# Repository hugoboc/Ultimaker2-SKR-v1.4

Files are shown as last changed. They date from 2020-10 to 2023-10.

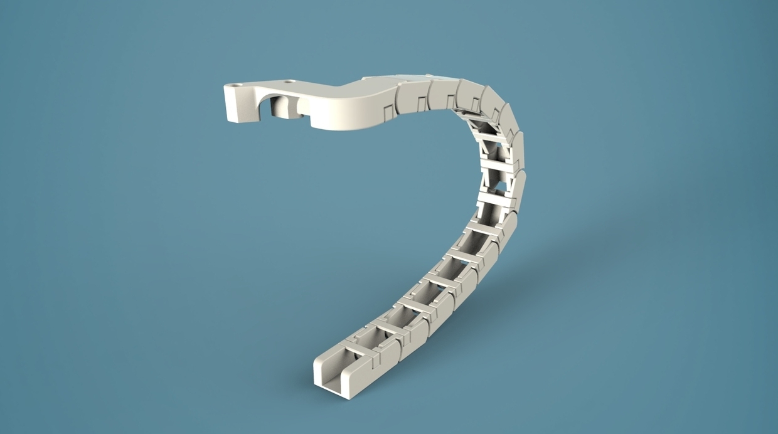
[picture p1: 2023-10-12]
01 CAD/03_z_stage_assembly/Ultimaker 2 Cable Chain/photos/UM2CC.jpg

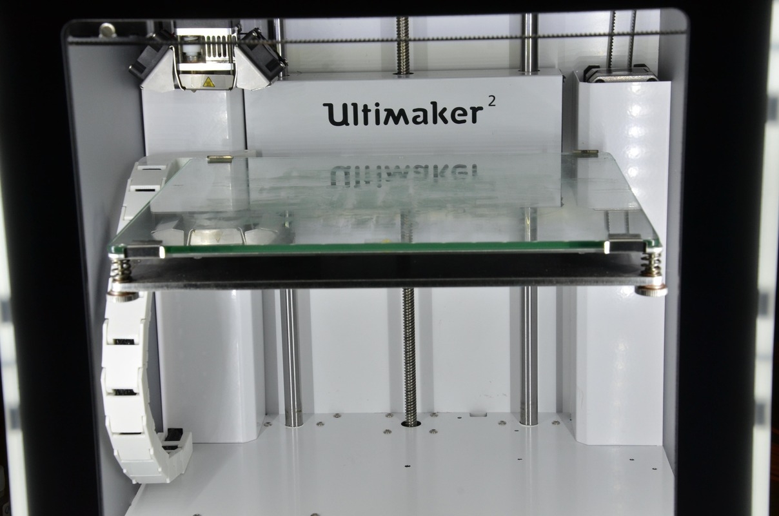
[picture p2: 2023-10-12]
01 CAD/03_z_stage_assembly/Ultimaker 2 Cable Chain/photos/um2_energyChain.jpg

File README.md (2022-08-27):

# Ultimaker 2 SKR v1.4 Turbo
all documentation needed to update Ultimaker 2 with a Bigtreetech SKR v1.4 32 bit board 

Features:

- HextrudOrt direct drive
- Optimized bed base plate to minimize vibrations
- 8mm print head shafts
- Custom sliding blocks
- Magnetic spring steel plate
- Z Probe for bed mesh leveling
- Klipper firmware

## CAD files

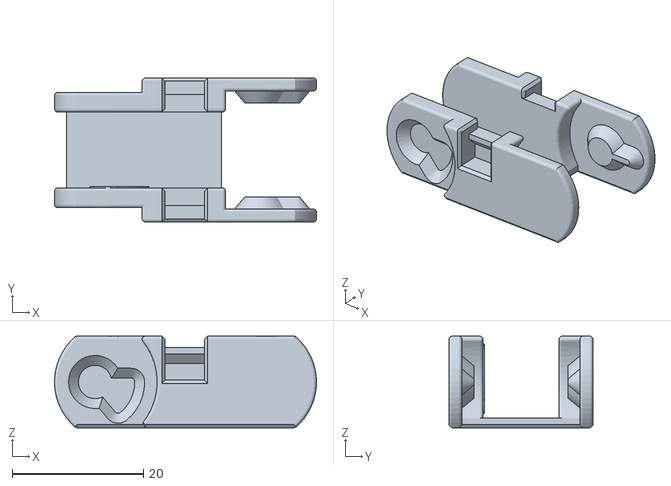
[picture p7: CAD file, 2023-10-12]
01 CAD/03_z_stage_assembly/Ultimaker 2 Cable Chain/UM2CableChain_ChainSegment.STL
40.0 x 22.0 x 14.0

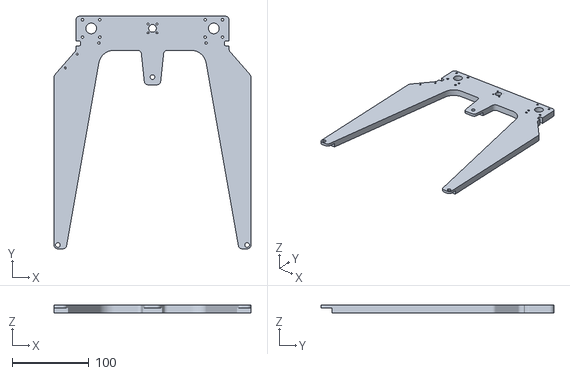
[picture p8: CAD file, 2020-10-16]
05 STLs/base_plate_optimized_10mm.stl
257.0 x 303.5 x 10.0

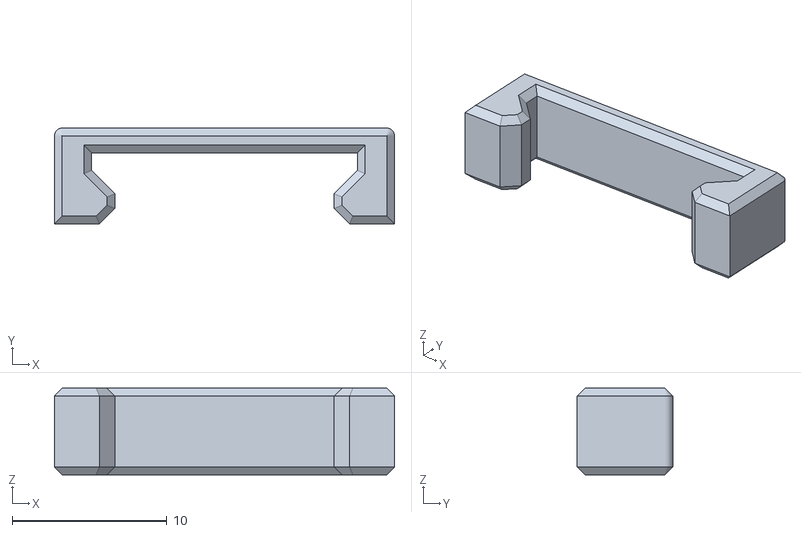
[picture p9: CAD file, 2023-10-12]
01 CAD/03_z_stage_assembly/Ultimaker 2 Cable Chain/UM2CableChain_Lid.STL
22.0 x 6.20 x 5.60

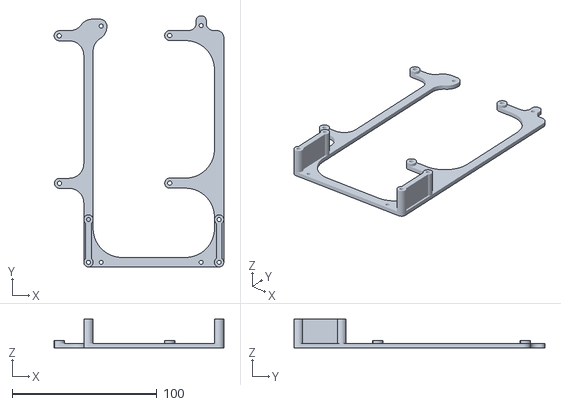
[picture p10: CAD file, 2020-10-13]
05 STLs/um2_skr14_holder.stl
117.2 x 173.2 x 20.0

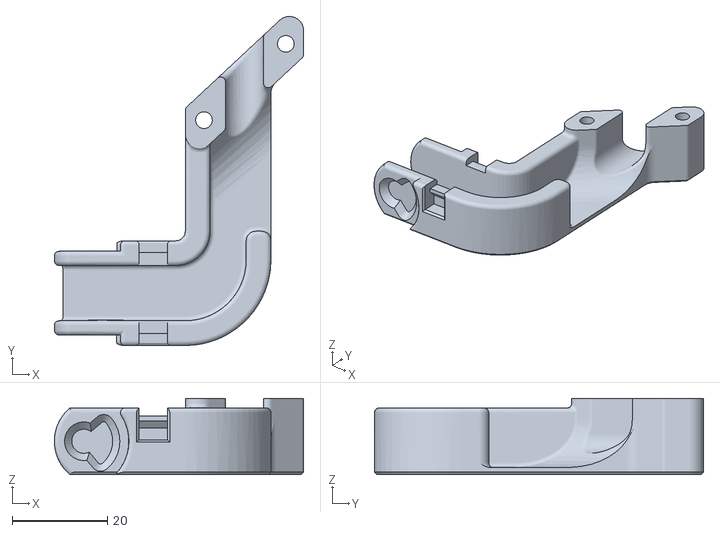
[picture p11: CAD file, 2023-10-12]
01 CAD/03_z_stage_assembly/Ultimaker 2 Cable Chain/UM2CableChain_BedEnd.STL
52.4 x 69.1 x 16.0

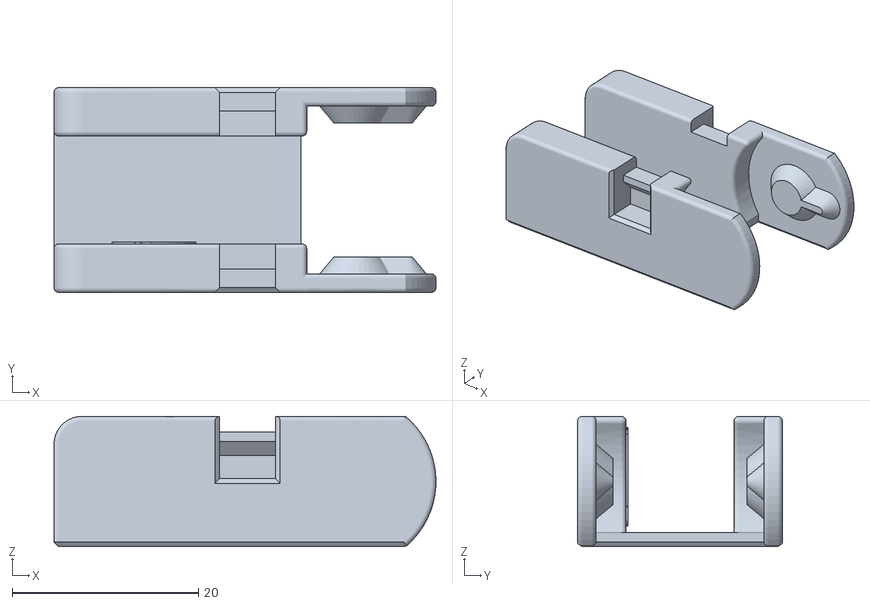
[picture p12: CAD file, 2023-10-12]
01 CAD/03_z_stage_assembly/Ultimaker 2 Cable Chain/UM2CableChain_BottomEnd.STL
41.0 x 22.0 x 14.0

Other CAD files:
01 CAD/03_z_stage_assembly/z-stage_assembly_2 v13.f3z

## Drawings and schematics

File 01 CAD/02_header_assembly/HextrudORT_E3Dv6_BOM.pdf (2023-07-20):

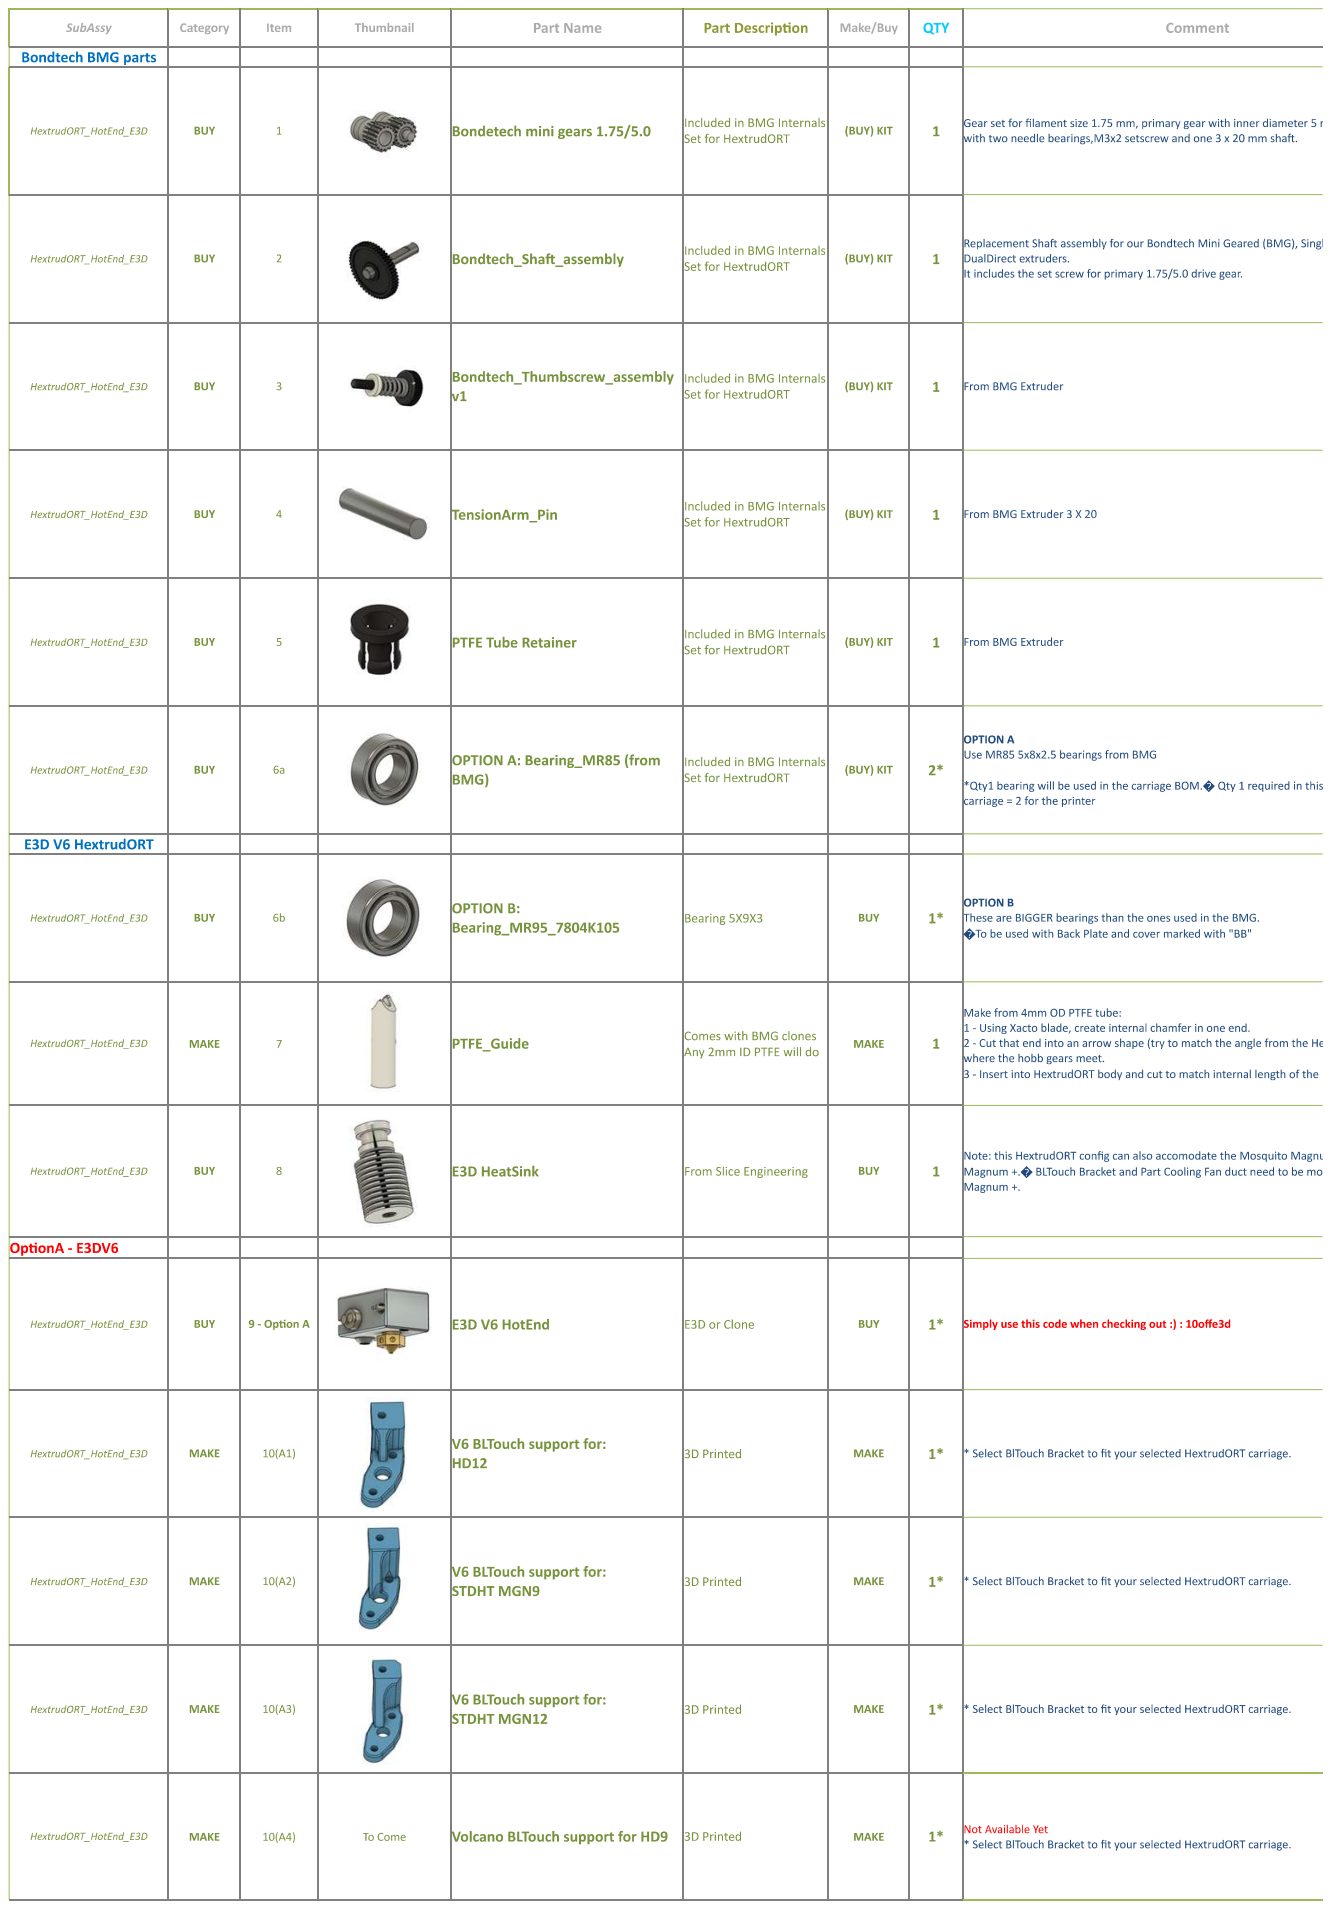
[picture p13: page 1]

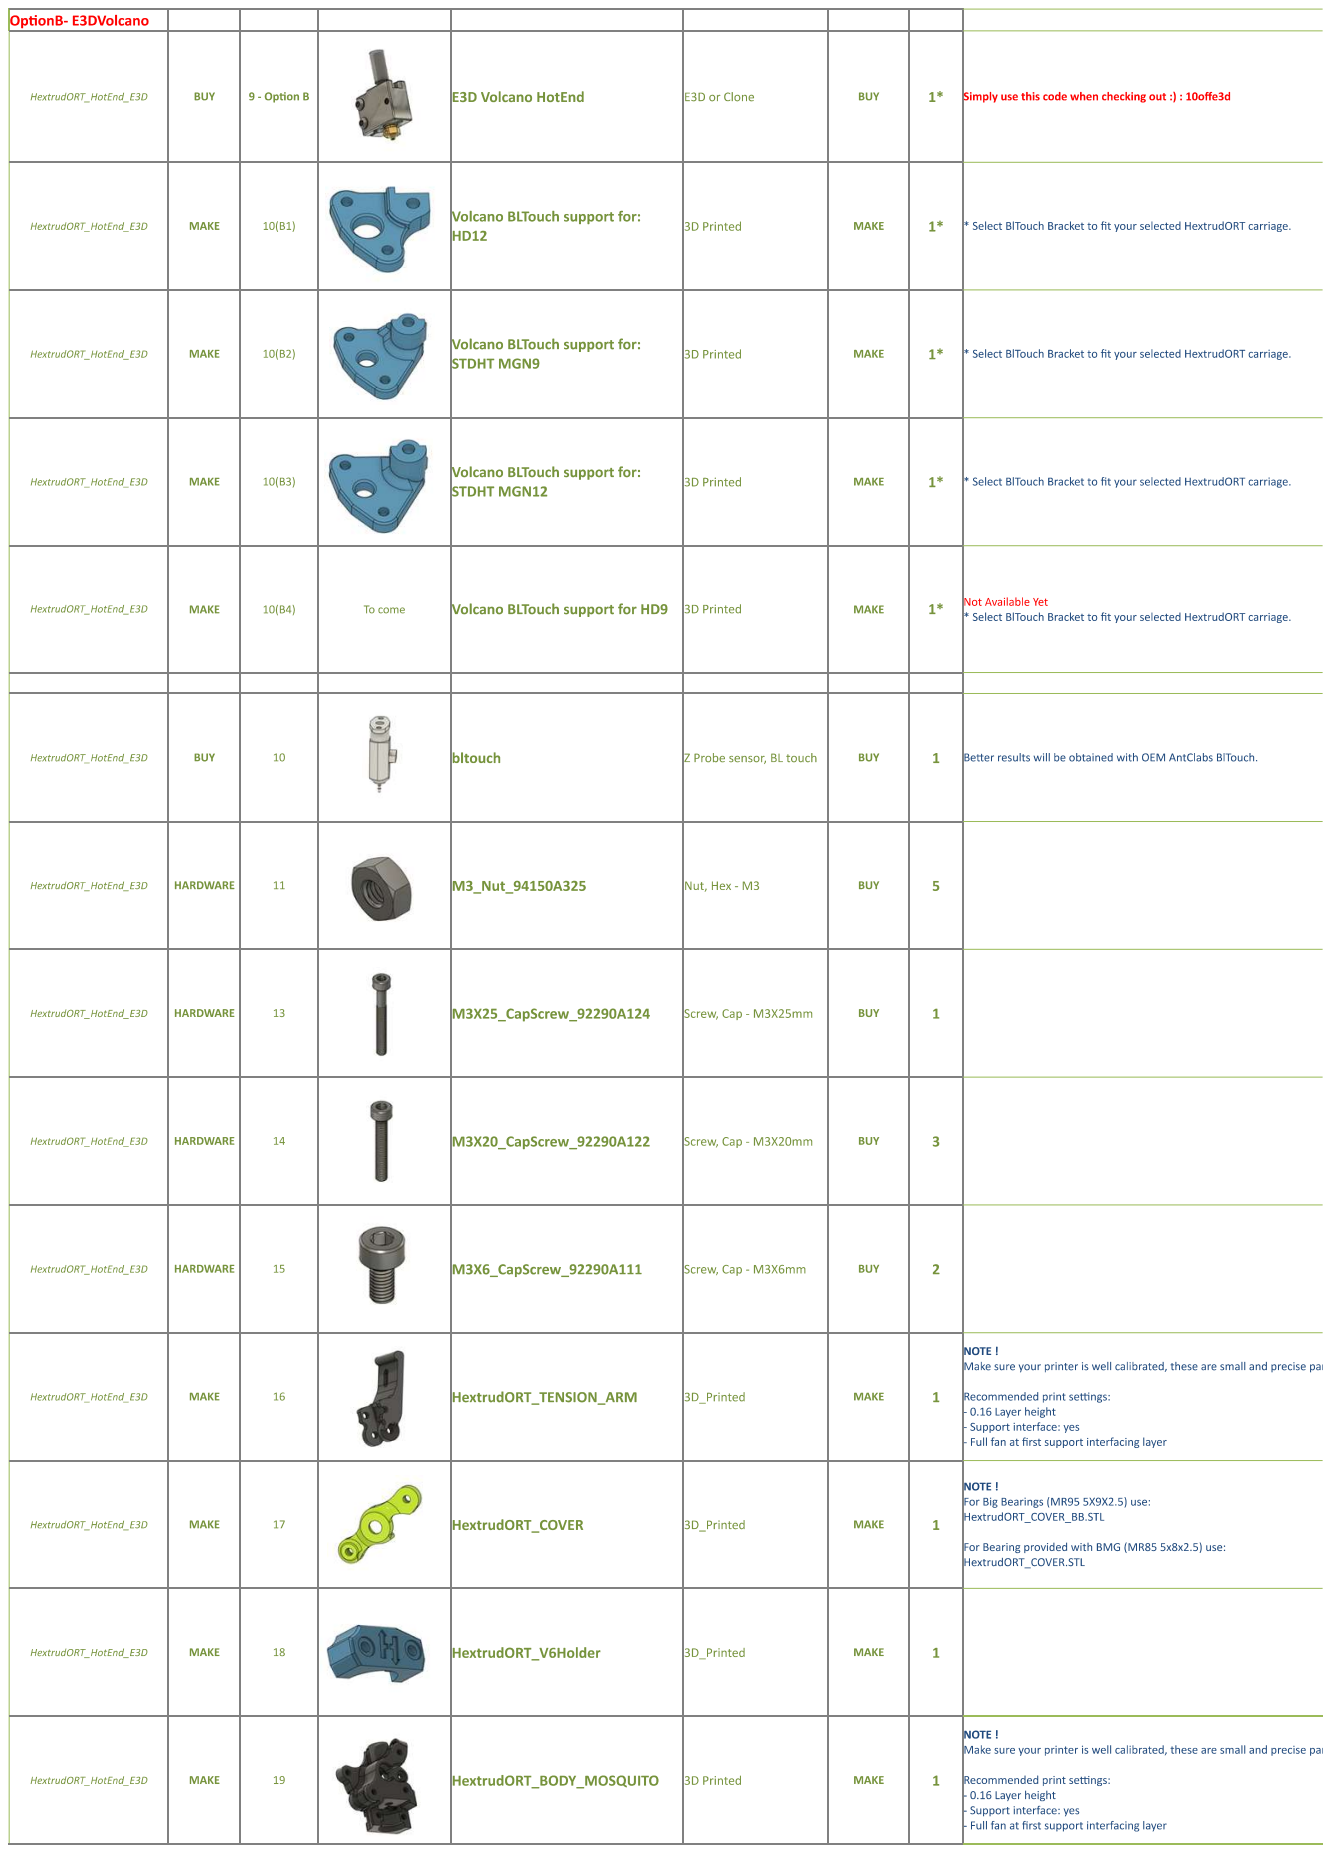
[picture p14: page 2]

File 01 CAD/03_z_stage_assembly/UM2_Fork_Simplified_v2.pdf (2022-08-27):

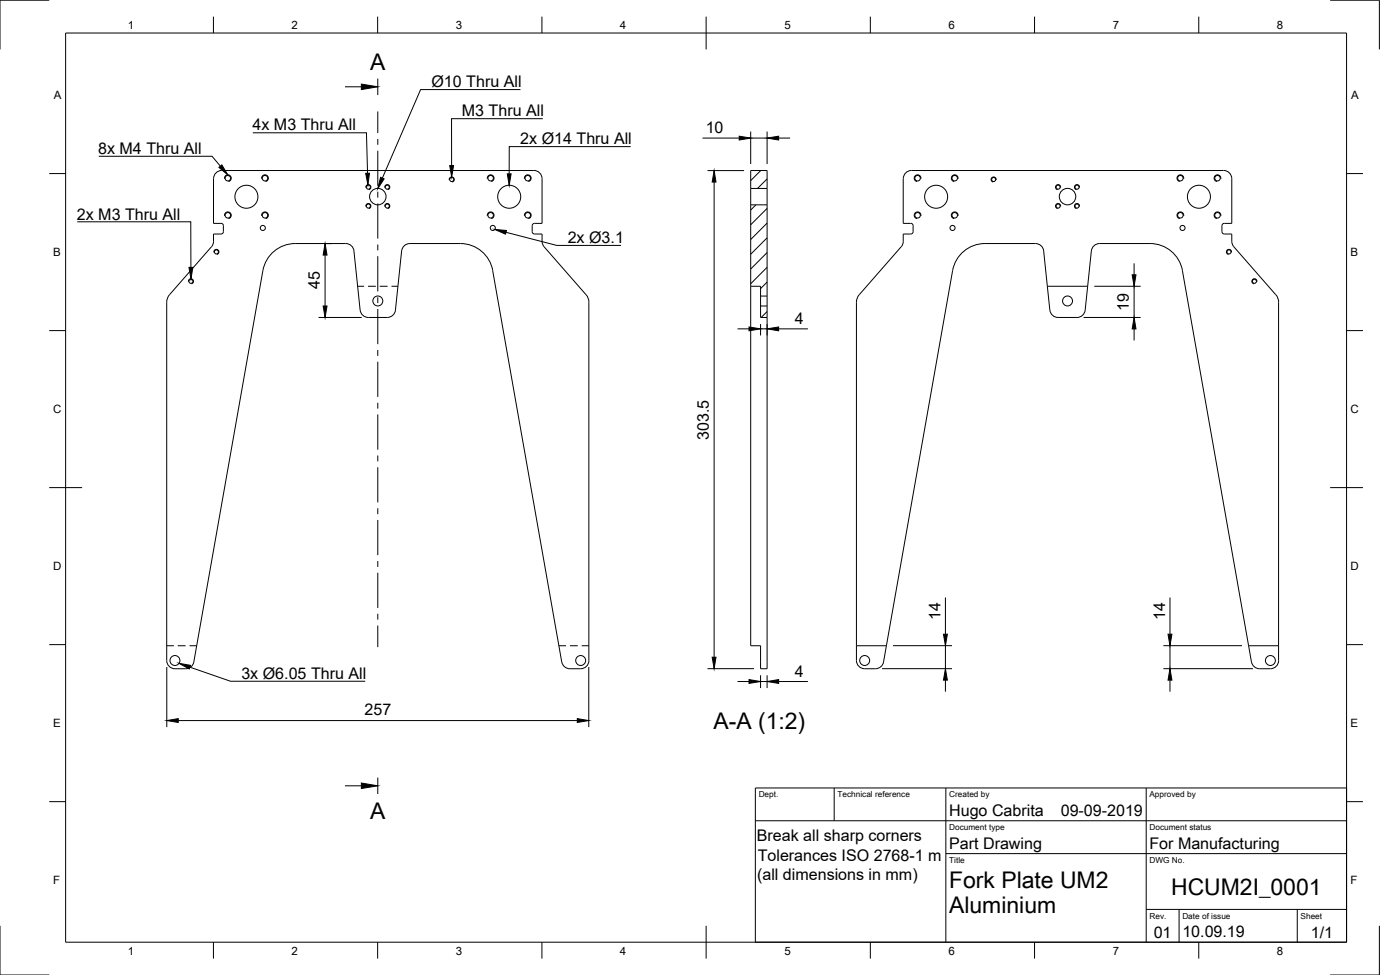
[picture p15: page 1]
8x M4 Thru All; 2x M3 Thru All; 3x Ø6.05 Thru All; 2x Ø14 Thru All; M3 Thru All; Ø10 Thru All; 4x M3 Thru All

Dept. | Technical reference | Created by Hugo Cabrita 09-09-2019 | Approved by

Break all sharp corners Tolerances ISO 2768-1 m (all dimensions in mm) | | Document type Part Drawing | Document status For Manufacturing

Title Fork Plate UM2 Aluminium | DWG No. HCUM2I_0001

Rev. 01 | Date of issue 10.09.19 | Sheet 1/1

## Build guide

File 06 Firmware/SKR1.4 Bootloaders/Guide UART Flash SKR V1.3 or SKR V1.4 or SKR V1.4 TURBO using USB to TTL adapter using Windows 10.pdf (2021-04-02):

Version 1.0 by GadgetAngel based on Sineos work

Just for future reference: Flashed a SKR 1.4 Turbo with @ardiehl Bootloader, using a USB to TTL adapter:
Things needed:
USB to TTL adapter, e.g. https://www.amazon.com/dp/B075N82CDL Some Jumper wires, e.g https://www.amazon.com/dp/B01EV70C78 female to female for the USB to TTL
female to male to conveniently contact the pin P2.10 to get the board into ISP mode
@ardiehl bootloader hex (attached to this post, or build it your self) (https://github.com/GadgetAngel/BTT_SKR_13_14_14T_SD-DFU-Bootloader/tree/main/bootloader_bin/compiled_bootloader_bin) Flashmagic (https://www.flashmagictool.com/download.html)
Procedure:
1. Power the board via USB or 12V / 24V
2. Contact the USB TTL adapter as shown in the picture (cyan arrows) RX of the adapter to TX on the board
TX of the adapter to RX on the board
GND to GND
3. Contact the SMD resistor (R28) to GND of the board (dark blue arrows), e.g. middle pin of an endstop (here the female to male jumper cable comes in handy). This will connect to the ISP_BOOT mode pin P2.10 (contact- Nr3).
4. Reset the board while holding the contact (Nr. 3)
5. Shortly after releasing the Reset button also remove the ISP connection (Nr. 3)
6. Start Flashmagic
Chose the @ardiehl hex file (https://github.com/GadgetAngel/BTT_SKR_13_14_14T_SD-DFU-Bootloader/tree/main/bootloader_bin/compiled_bootloader_bin)

# Sineos commented 15 days ago:

## How to backup and restore SKR 1.4 /turbo & SKR 1.3 boards

## Using a USB to TTL Adapter:

Guide to backup and restore SKR 1.4 / turbo (1.3 also work) via UART by USB to TTL adapter. Useful to try to fix corrupted
boot loader and no update from SD problem or simply backup. I, GadgetAngel, have tried to find other ways of doing this with the LPC1768 or LPC1769 and the only method that works is using the embedded boot loader and USART0 communication. I could never get an ST-LINK-V2 clone to work!

(I’m not responsible for any damage, do so at your own risk)

ORIGINAL URL: https://github.com/bigtreetech/BIGTREETECH-SKR-V1.3/issues/346#issuecomment-754120640

Set the correct COM port for your USB to TTL adapter (look it up in the windows device manager)
Set the correct chip type (LPC1769 for SKR 1.4 Turbo)
Set Erase to Sectors used by file
Press start
7. Wait until finished, then reset the board
8. Flash new firmware.bin , e.g. via SD card upload or using the new bootloader's direct flash capabilities
Flashing via STLink v2 did not work for me, neither from linux shell, nor via PlatformIO but the Flashmagic way was surprisingly painless.

# Bootloader Hex (unzip to use):

DFU-Bootloader.zip (https://github.com/bigtreetech/BIGTREETECH-SKR-V1.3/files/5766031/DFU-Bootloader.zip)

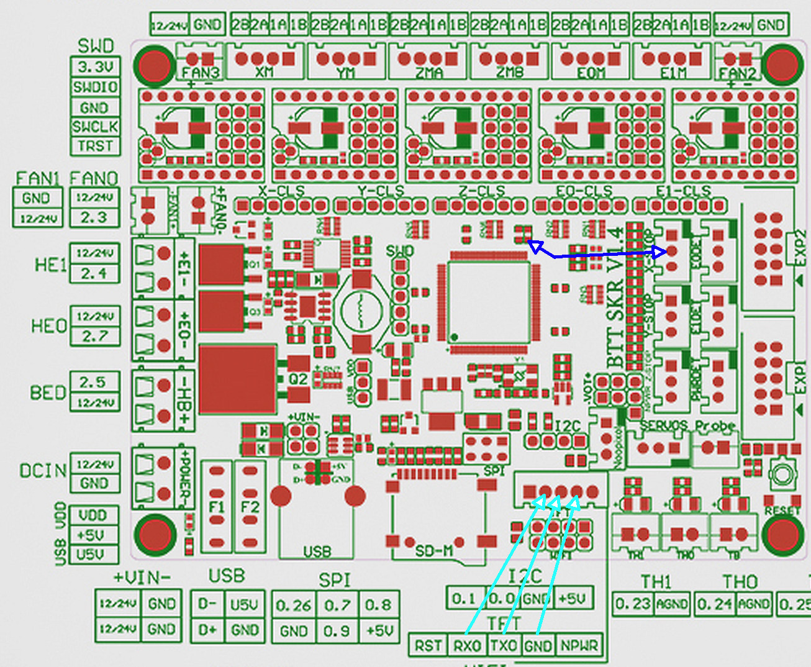
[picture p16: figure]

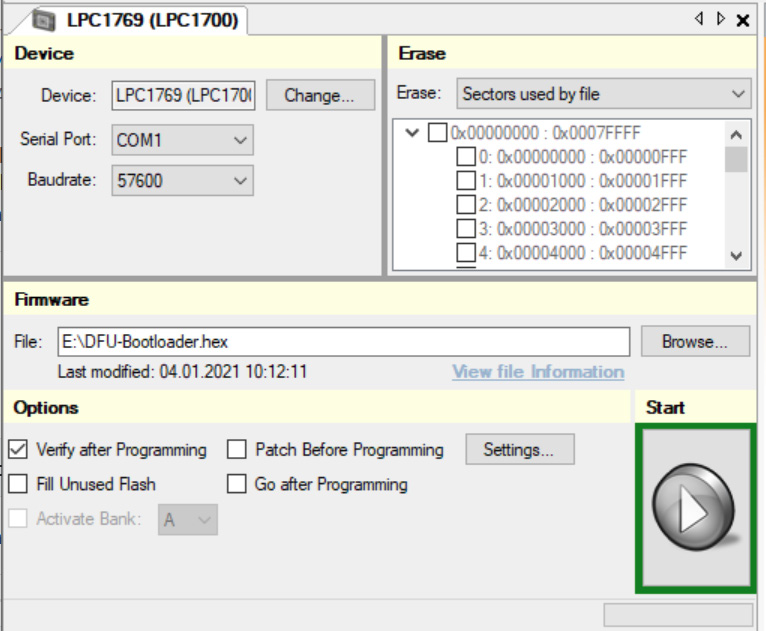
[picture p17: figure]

## Edit for SKR Board 1.3: For SKR 1.3 simply connect AUX-1 in Step 2 and use (read short) the

BOOT Jumper pins to achieve the same as in Step 3 to 5.

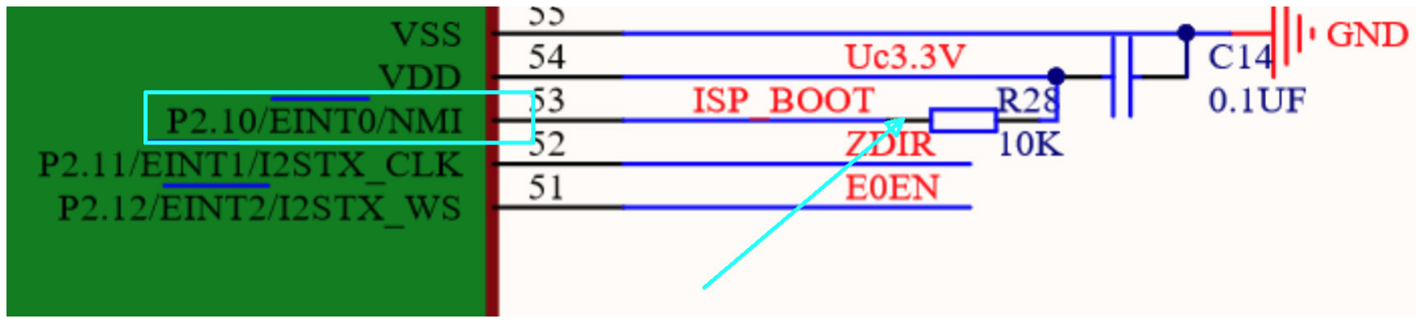
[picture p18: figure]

- So you need to make this contact between GND and P2.10 and hold it, reset the board and then quickly after releasing the reset button remove the contact.

## - To get the chip into the ISP mode you need to pull the pin P2.10 to GND during reset

- The P2.10 is easily accessible via the bottom of the SMD resistor
- GND is easily accessible via, e.g. the middle endstop pin

# IMPORTANT: It needs further explanation about ISP_BOOT PIN needing to be held to low during a board reset so the embedded boot loader will become active:

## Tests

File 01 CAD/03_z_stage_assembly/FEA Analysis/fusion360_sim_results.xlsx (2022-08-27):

Part Name | Material | displacement 2.1N | displacement 2.1N change | displacement 300g | displacement 300g change | modal frequency 1 | modal frequency change | Part Weight | weight change
Original 4mm | Aluminium 6061 | 1.190 | - | 0.170 | - | 39 | - | 0.797 | -
Original 10mm | Aluminium 6061 | 0.079 | -93.33613445% | 0.011 | -93.52941176% | 97 | 148.7179487% | 1.993 | 150.0627353%
Optimized (V3) Alu - 10mm | Aluminium 6061 | 0.220 | -81.51260504% | 0.031 | -81.76470588% | 133 | 241.025641% | 0.797 | 0%
Optimized (V3) Alu - 8mm | Aluminium 6061 | 0.426 | -64.20168067% | 0.061 | -64.11764706% | 107 | 174.3589744% | 0.612 | -23.21204517%
Optimized (V3) Steel - 10mm | Steel - High Strength | 0.076 | -93.62184874% | 0.011 | -93.64705882% | 132 | 238.4615385% | 2.226 | 179.2973651%
Optimized (V3) Steel - 8mm | Steel - High Strength | 0.147 | -87.63865546% | 0.021 | -87.64705882% | 106 | 171.7948718% | 1.781 | 123.4629862%

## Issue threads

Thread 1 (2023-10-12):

follow up questions

totoantibes, 2023-10-12:
Hi this is a very interesting build indeed. i have a few basic questions though.

1) I saw [here](https://community.ultimaker.com/topic/30786-ultimaker-with-skr-14/) that people had to splice the LCD cable in order to get it the correct 3.3 Voltage. Is that not needed? or is that achieved with jumpers somewhere?
2) is there a need for the UM2 Power USB Power Switch adapter interface in order to keep the "holes" on the original case for the power, switch  and usb plug?
3) the UM2 PT100 can then be plugged directly onto the board without amp circuit?

Merci

hugoboc, 2023-10-12:
Hi @totoantibes,

1. I am using Klipper, so I don't use an LCD anymore. I use the Mainsail web interface on my PC or phone to interact with the printer.
2. You don't need one, and I don't think they are for sale anymore (I bought it on Aliexpress). At the time I wanted to keep on using the original UM2 power brick, so I opted for this solution. Now, you'll probably have to buy a power source, but in this case, I think you'll need to modify the "holes" in the back.
3. Yes, but I bought new thermistors (bed and hotend), which I connected directly to the SKR1.4. I've updated the documentation and added which thermistors I have installed.

Documentation in the repo is not so well organized and some things are missing. I'll do some housekeeping in the next few days.

De rien :)

Let me know if you have any more questions.

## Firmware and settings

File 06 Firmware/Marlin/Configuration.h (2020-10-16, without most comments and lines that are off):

#pragma once
#define CONFIGURATION_H_VERSION 020007
#define STRING_CONFIG_H_AUTHOR "(Hugo Cabrita SKR1.4 03.10.2020)" // Who made the changes.
#define SHOW_BOOTSCREEN
#define SERIAL_PORT -1
#define SERIAL_PORT_2 0
#define BAUDRATE 250000
  #define MOTHERBOARD BOARD_BTT_SKR_V1_4_TURBO
#define CUSTOM_MACHINE_NAME "UM2 SKR1.4"
#define EXTRUDERS 1
#define DEFAULT_NOMINAL_FILAMENT_DIA 1.75
#define TEMP_SENSOR_0 5
#define TEMP_SENSOR_1 0
#define TEMP_SENSOR_2 0
#define TEMP_SENSOR_3 0
#define TEMP_SENSOR_4 0
#define TEMP_SENSOR_5 0
#define TEMP_SENSOR_6 0
#define TEMP_SENSOR_7 0
#define TEMP_SENSOR_BED 5
#define TEMP_SENSOR_PROBE 0
#define TEMP_SENSOR_CHAMBER 0
#define DUMMY_THERMISTOR_998_VALUE 25
#define DUMMY_THERMISTOR_999_VALUE 100
#define MAX_REDUNDANT_TEMP_SENSOR_DIFF 10
#define TEMP_RESIDENCY_TIME     10  // (seconds) Time to wait for hotend to "settle" in M109
#define TEMP_WINDOW              1  // (°C) Temperature proximity for the "temperature reached" timer
#define TEMP_HYSTERESIS          3  // (°C) Temperature proximity considered "close enough" to the target
#define TEMP_BED_RESIDENCY_TIME 10  // (seconds) Time to wait for bed to "settle" in M190
#define TEMP_BED_WINDOW          1  // (°C) Temperature proximity for the "temperature reached" timer
#define TEMP_BED_HYSTERESIS      3  // (°C) Temperature proximity considered "close enough" to the target
#define HEATER_0_MINTEMP   5
#define HEATER_1_MINTEMP   5
#define HEATER_2_MINTEMP   5
#define HEATER_3_MINTEMP   5
#define HEATER_4_MINTEMP   5
#define HEATER_5_MINTEMP   5
#define HEATER_6_MINTEMP   5
#define HEATER_7_MINTEMP   5
#define BED_MINTEMP        5
#define HEATER_0_MAXTEMP 255
#define HEATER_1_MAXTEMP 275
#define HEATER_2_MAXTEMP 275
#define HEATER_3_MAXTEMP 275
#define HEATER_4_MAXTEMP 275
#define HEATER_5_MAXTEMP 275
#define HEATER_6_MAXTEMP 275
#define HEATER_7_MAXTEMP 275
#define BED_MAXTEMP      100
#define PIDTEMP
#define BANG_MAX 255     // Limits current to nozzle while in bang-bang mode; 255=full current
#define PID_MAX BANG_MAX // Limits current to nozzle while PID is active (see PID_FUNCTIONAL_RANGE below); 255=full current
#define PID_K1 0.95      // Smoothing factor within any PID loop
    #define DEFAULT_Kp  22.20
    #define DEFAULT_Ki   1.08
    #define DEFAULT_Kd 114.00
#define MAX_BED_POWER 255 // limits duty cycle to bed; 255=full current
  #define PID_FUNCTIONAL_RANGE 10 // If the temperature difference between the target temperature and the actual temperature
#define PREVENT_COLD_EXTRUSION
#define EXTRUDE_MINTEMP 170
#define PREVENT_LENGTHY_EXTRUDE
#define EXTRUDE_MAXLENGTH 200
#define THERMAL_PROTECTION_HOTENDS // Enable thermal protection for all extruders
#define THERMAL_PROTECTION_BED     // Enable thermal protection for the heated bed
#define THERMAL_PROTECTION_CHAMBER // Enable thermal protection for the heated chamber
#define USE_XMIN_PLUG
#define USE_YMAX_PLUG
#define USE_ZMAX_PLUG
#define ENDSTOPPULLUPS
#define X_MIN_ENDSTOP_INVERTING false // Set to true to invert the logic of the endstop.
#define Y_MIN_ENDSTOP_INVERTING false // Set to true to invert the logic of the endstop.
#define Z_MIN_ENDSTOP_INVERTING true // Set to true to invert the logic of the endstop.
#define X_MAX_ENDSTOP_INVERTING false // Set to true to invert the logic of the endstop.
#define Y_MAX_ENDSTOP_INVERTING false // Set to true to invert the logic of the endstop.
#define Z_MAX_ENDSTOP_INVERTING true // Set to true to invert the logic of the endstop.
#define Z_MIN_PROBE_ENDSTOP_INVERTING true // Set to true to invert the logic of the probe.
#define X_DRIVER_TYPE  TMC2209
#define Y_DRIVER_TYPE  TMC2209
#define Z_DRIVER_TYPE  TMC2209
#define E0_DRIVER_TYPE TMC2209
#define DEFAULT_AXIS_STEPS_PER_UNIT   { 80, 80, 200, 805.68 }
#define DEFAULT_MAX_FEEDRATE          { 300, 300, 40, 45 }
#define DEFAULT_MAX_ACCELERATION      { 500, 500, 100, 10000 }
#define DEFAULT_ACCELERATION          3000    // X, Y, Z and E acceleration for printing moves
#define DEFAULT_RETRACT_ACCELERATION  3000    // E acceleration for retracts
#define DEFAULT_TRAVEL_ACCELERATION   3000    // X, Y, Z acceleration for travel (non printing) moves
#define DEFAULT_EJERK    5.0  // May be used by Linear Advance
  #define JUNCTION_DEVIATION_MM 0.013 // (mm) Distance from real junction edge
  #define JD_HANDLE_SMALL_SEGMENTS    // Use curvature estimation instead of just the junction angle
#define Z_MIN_PROBE_USES_Z_MIN_ENDSTOP_PIN
#define NOZZLE_TO_PROBE_OFFSET { 10, 10, 0 }
#define PROBING_MARGIN 10
#define XY_PROBE_SPEED (133*60)
#define Z_PROBE_SPEED_FAST HOMING_FEEDRATE_Z
#define Z_PROBE_SPEED_SLOW (Z_PROBE_SPEED_FAST / 2)
#define Z_CLEARANCE_DEPLOY_PROBE   10 // Z Clearance for Deploy/Stow
#define Z_CLEARANCE_BETWEEN_PROBES  5 // Z Clearance between probe points
#define Z_CLEARANCE_MULTI_PROBE     5 // Z Clearance between multiple probes
#define Z_PROBE_LOW_POINT          -2 // Farthest distance below the trigger-point to go before stopping
#define Z_PROBE_OFFSET_RANGE_MIN -20
#define Z_PROBE_OFFSET_RANGE_MAX 20
#define X_ENABLE_ON 0
#define Y_ENABLE_ON 0
#define Z_ENABLE_ON 0
#define E_ENABLE_ON 0 // For all extruders
#define DISABLE_X false
#define DISABLE_Y false
#define DISABLE_Z false
#define DISABLE_E false             // Disable the extruder when not stepping
#define DISABLE_INACTIVE_EXTRUDER   // Keep only the active extruder enabled
#define INVERT_X_DIR true
#define INVERT_Y_DIR false
#define INVERT_Z_DIR true
#define INVERT_E0_DIR false
#define INVERT_E1_DIR false
#define INVERT_E2_DIR false
#define INVERT_E3_DIR false
#define INVERT_E4_DIR false
#define INVERT_E5_DIR false
#define INVERT_E6_DIR false
#define INVERT_E7_DIR false
#define Z_HOMING_HEIGHT  4      // (mm) Minimal Z height before homing (G28) for Z clearance above the bed, clamps, ...
#define X_HOME_DIR -1
#define Y_HOME_DIR 1
#define Z_HOME_DIR 1
#define X_BED_SIZE 200
#define Y_BED_SIZE 208
#define X_MIN_POS 0
#define Y_MIN_POS 0
#define Z_MIN_POS 0
#define X_MAX_POS X_BED_SIZE
#define Y_MAX_POS Y_BED_SIZE
#define Z_MAX_POS 200
#define MIN_SOFTWARE_ENDSTOPS
  #define MIN_SOFTWARE_ENDSTOP_X
  #define MIN_SOFTWARE_ENDSTOP_Y
#define MAX_SOFTWARE_ENDSTOPS
  #define MAX_SOFTWARE_ENDSTOP_X
  #define MAX_SOFTWARE_ENDSTOP_Y
  #define MAX_SOFTWARE_ENDSTOP_Z
#define MESH_BED_LEVELING
#define RESTORE_LEVELING_AFTER_G28
  #define ENABLE_LEVELING_FADE_HEIGHT
  #define SEGMENT_LEVELED_MOVES
  #define LEVELED_SEGMENT_LENGTH 5.0 // (mm) Length of all segments (except the last one)
  #define MESH_INSET 10          // Set Mesh bounds as an inset region of the bed
  #define GRID_MAX_POINTS_X 5    // Don't use more than 7 points per axis, implementation limited.
  #define GRID_MAX_POINTS_Y GRID_MAX_POINTS_X
#define HOMING_FEEDRATE_XY (60*60)
#define HOMING_FEEDRATE_Z  (40*60)
#define VALIDATE_HOMING_ENDSTOPS
#define EEPROM_SETTINGS     // Persistent storage with M500 and M501
#define EEPROM_CHITCHAT       // Give feedback on EEPROM commands. Disable to save PROGMEM.
#define EEPROM_BOOT_SILENT    // Keep M503 quiet and only give errors during first load
#define HOST_KEEPALIVE_FEATURE        // Disable this if your host doesn't like keepalive messages
#define DEFAULT_KEEPALIVE_INTERVAL 2  // Number of seconds between "busy" messages. Set with M113.
#define BUSY_WHILE_HEATING            // Some hosts require "busy" messages even during heating
#define PREHEAT_1_LABEL       "PLA"
#define PREHEAT_1_TEMP_HOTEND 215
#define PREHEAT_1_TEMP_BED     60
#define PREHEAT_1_FAN_SPEED     0 // Value from 0 to 255
#define PREHEAT_2_LABEL       "ABS"
#define PREHEAT_2_TEMP_HOTEND 240
#define PREHEAT_2_TEMP_BED    70
#define PREHEAT_2_FAN_SPEED     0 // Value from 0 to 255
#define PRINTJOB_TIMER_AUTOSTART
#define LCD_LANGUAGE en
#define DISPLAY_CHARSET_HD44780 JAPANESE
#define LCD_INFO_SCREEN_STYLE 0
#define SDSUPPORT
#define SPEAKER
#define SOFT_PWM_SCALE 0
#define SERVO_DELAY { 300 }

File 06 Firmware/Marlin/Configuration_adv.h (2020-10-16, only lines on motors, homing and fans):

#define E0_AUTO_FAN_PIN -1
#define E1_AUTO_FAN_PIN -1
#define E2_AUTO_FAN_PIN -1
#define E3_AUTO_FAN_PIN -1
#define E4_AUTO_FAN_PIN -1
#define E5_AUTO_FAN_PIN -1
#define E6_AUTO_FAN_PIN -1
#define E7_AUTO_FAN_PIN -1
#define CHAMBER_AUTO_FAN_PIN -1
#define HOMING_BUMP_MM      { 0, 0, 2 }       // (mm) Backoff from endstops after first bump
#define HOMING_BUMP_DIVISOR { 2, 2, 4 }       // Re-Bump Speed Divisor (Divides the Homing Feedrate)
#define MICROSTEP_MODES { 16, 16, 16, 16, 16, 16 } // [1,2,4,8,16]
#define LIN_ADVANCE
  #define LIN_ADVANCE_K 0.22    // Unit: mm compression per 1mm/s extruder speed
    #define X_CURRENT       800        // (mA) RMS current. Multiply by 1.414 for peak current.
    #define X_CURRENT_HOME  X_CURRENT  // (mA) RMS current for sensorless homing
    #define X_MICROSTEPS     16    // 0..256
    #define Y_CURRENT       800
    #define Y_CURRENT_HOME  Y_CURRENT
    #define Y_MICROSTEPS     16
    #define Z_CURRENT       800
    #define Z_CURRENT_HOME  Z_CURRENT
    #define Z_MICROSTEPS     16
    #define E0_CURRENT      800
    #define E0_MICROSTEPS    16
    #define CURRENT_STEP_DOWN     50  // [mA]
    #define REPORT_CURRENT_CHANGE
  #define X_HYBRID_THRESHOLD     100  // [mm/s]
  #define X2_HYBRID_THRESHOLD    100
  #define Y_HYBRID_THRESHOLD     100
  #define Y2_HYBRID_THRESHOLD    100
  #define Z_HYBRID_THRESHOLD       3
  #define Z2_HYBRID_THRESHOLD      3
  #define Z3_HYBRID_THRESHOLD      3
  #define Z4_HYBRID_THRESHOLD      3
  #define E0_HYBRID_THRESHOLD     30
  #define E1_HYBRID_THRESHOLD     30
  #define E2_HYBRID_THRESHOLD     30
  #define E3_HYBRID_THRESHOLD     30
  #define E4_HYBRID_THRESHOLD     30
  #define E5_HYBRID_THRESHOLD     30
  #define E6_HYBRID_THRESHOLD     30
  #define E7_HYBRID_THRESHOLD     30
  #define SENSORLESS_HOMING // StallGuard capable drivers only
    #define X_STALL_SENSITIVITY  90
    #define X2_STALL_SENSITIVITY X_STALL_SENSITIVITY
    #define Y_STALL_SENSITIVITY  100
    #define Y2_STALL_SENSITIVITY Y_STALL_SENSITIVITY

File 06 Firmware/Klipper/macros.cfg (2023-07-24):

#  ___  ___  ___  _____ ______ _____ _
#  |  \/  | / _ \/  __ \| ___ \  _  ( )
#  | .  . |/ /_\ \ /  \/| |_/ / | | |/ ___
#  | |\/| ||  _  | |    |    /| | | | / __|
#  | |  | || | | | \__/\| |\ \\ \_/ / \__ \
#  \_|  |_/\_| |_/\____/\_| \_|\___/  |___/
#

# # # # # # # # # # # # # # # # # # #
# Printer start and stop
# # # # # # # # # # # # # # # # # # #
#

[gcode_macro _CHECK_BED_MESH]
gcode:
  G28 					                      # home all axes
  {% if printer.bed_mesh.profile_name == '' %}
  M118 Mesh does not exist, creating new
  G90                                    # Set all axes to absolute
  BED_MESH_CLEAR
  G1 Z2 F1000 				               # lower
  # G4 P120000
  BED_MESH_CALIBRATE PRINT_MIN={params.PRINT_MIN} PRINT_MAX={params.PRINT_MAX}
  M118 Mesh calibration finished
  UPDATE_DELAYED_GCODE ID=_AFTER_BED_CAL DURATION=1
  _NOZZLE_PURGE
  {%else %}
  M118 Mesh loaded
  #BED_MESH_PROFILE LOAD=default
  BED_MESH_PROFILE LOAD={printer.bed_mesh.profile_name}
  _NOZZLE_PURGE
  {% endif %}

[gcode_macro BED_CAL]
gcode:
  G90                                    # Set all axes to absolute
  BED_MESH_CLEAR
  G1 Z2 F1000 				               # lower
  # G4 P120000
  BED_MESH_CALIBRATE
  M118 Mesh calibration finished
  UPDATE_DELAYED_GCODE ID=_AFTER_BED_CAL DURATION=1

[delayed_gcode _AFTER_BED_CAL]
gcode:
  {% if printer.print_stats.state == 'standby' %}
  M118 Printer State is: {printer.print_stats.state}
  M118 Homing
  G28
  {%else %}
  M118 Printer State is: {printer.print_stats.state}
  {% endif %}

[gcode_macro _NOZZLE_PURGE]
gcode:
  {% set pos     = printer.toolhead.position     %}
  M220 S100                                # Reset speed
  G90                                      # Set all axes to absolute
  G92 E0 				                   # zero the extruded length again
  G1 Z80 F1000 				               # lower
  # G1 X190 F2000                            # Move to corner if not there already
  G1 X0 Y197 F6000                            # Move to corner if not there already
  G1 E80 F200 				               # purge nozzle quickly
  G92 E0 				                   # zero the extruded length again
  {% if pos.x <= 30 %}
  M118 Starting line purge
  G1 X0 Y100 Z0.2  F1500 			          # pull away filament
  {%else %}
  M118 Starting line purge
  # G1 X190 Y100 Z0.2  F2000 			       # pull away filament
  G1 X0 Y100 Z0.2  F1500 			       # pull away filament
  {% endif %}
  G1 Y3 E12 F600			               # move x-carriage 100mm while extruding
  G1 F9000				                   # set movement speed
  G92 E0				                   # zero the extruded length again
  SKEW_PROFILE LOAD=my_skew_profile        # Load skew profile

[gcode_macro _END_PRINT]
gcode:
  SET_SKEW CLEAR=1			# clear skew profile
  SET_PRESSURE_ADVANCE ADVANCE=0.000
  M104 S0 				# extruder heater off
  M140 S0 				# heated bed heater off (if you have it)
  G91 					# relative positioning
  G1 E-1 F300  				# retract the filament a bit before lifting the nozzle, to release some of the pressure
  # G1 Z+0.5 E-20 X-20 Y-20 F9000 		# move Z up a bit and retract filament even more
  G28 Z   				# move Z to min endstops, so the head is out of the way
  G28 X Y

  M84 					# steppers off
  G90 					# absolute positioning
  SET_LED LED=caselight WHITE=0.00 SYNC=0 TRANSMIT=1
  
[gcode_macro CANCEL_PRINT]
description: Cancel the actual running print
rename_existing: CANCEL_PRINT_BASE
gcode:
  SET_SKEW CLEAR=1			# clear skew profile
  SET_PRESSURE_ADVANCE ADVANCE=0.000
  G28 Z   				# move Z to min endstops, so the head is out of the way
  G28 X Y
  G91 					# relative positioning
  G1 E-20 F300  				# retract the filament a bit before lifting the nozzle, to release some of the pressure
  M104 S0 				# extruder heater off
  M140 S0 				# heated bed heater off (if you have it)
  M84 					# steppers off
  G90 					# absolute positioning
  RESTART


[gcode_macro PAUSE]
description: Pause the actual running print
rename_existing: PAUSE_BASE
gcode:
    ##### set defaults #####
    {% set x = params.X|default(0) %}      #edit to your park position
    {% set y = params.Y|default(197) %}      #edit to your park position
    {% set z = params.Z|default(10)|float %} #edit to your park position
    {% set e = params.E|default(2) %}        #edit to your retract length
    ##### calculate save lift position #####
    {% set max_z = printer.toolhead.axis_maximum.z|float %}
    {% set act_z = printer.toolhead.position.z|float %}
    {% set lift_z = z|abs %}
    {% if act_z < (max_z - lift_z) %}
        {% set z_safe = lift_z %}
    {% else %}
        {% set z_safe = max_z - act_z %}
    {% endif %}
    ##### end of definitions #####
    PAUSE_BASE
    G91
    {% if printer.extruder.can_extrude|lower == 'true' %}
      G1 E-{e} F2100
    {% else %}
      {action_respond_info("Extruder not hot enough")}
    {% endif %}
    {% if "xyz" in printer.toolhead.homed_axes %}    
      G1 Z{z_safe}
      G90
      G1 X{x} Y{y} F6000
    {% else %}
      {action_respond_info("Printer not homed")}
    {% endif %}

[gcode_macro RESUME]
description: Resume the actual running print
rename_existing: RESUME_BASE
gcode:
    ##### set defaults #####
    {% set e = params.E|default(2) %} #edit to your retract length
    #### get VELOCITY parameter if specified ####
    {% if 'VELOCITY' in params|upper %}
      {% set get_params = ('VELOCITY=' + params.VELOCITY)  %}
    {%else %}
      {% set get_params = "" %}
    {% endif %}
    ##### end of definitions #####
    G91
    {% if printer.extruder.can_extrude|lower == 'true' %}
      G1 E{e} F2100
    {% else %}
      {action_respond_info("Extruder not hot enough")}
    {% endif %}  
    RESUME_BASE {get_params}

# # # # # # # # # # # # # # # # # # #
# Calibrations
# # # # # # # # # # # # # # # # # # #

[gcode_macro ENDSTOP_CAL]
gcode:
  G28
  ENDSTOP_PHASE_CALIBRATE
  G91
  #G1 x100 y-100 z-10 F2000
  G1 z-10 F1500
  G90
  G28
  G91
  #G1 x150 y-190 z-40 F2000
  G1 z-40 F1500
  G90
  G28
  G91
  #G1 x10 y-120 z-120 F2000
  G1 z-120 F1500
  G90
  G28
  G91
  #G1 x190 y-20 z-80 F2000
  G1 z-80 F1500
  G90
  G28
  G91
  #G1 x55 y-100 z-60 F2000
  G1 z-60 F1500
  G90
  G28
  G91
  #G1 x30 y-170 z-50 F2000
  G1 z-50 F1500
  G28
  G90
  ENDSTOP_PHASE_CALIBRATE STEPPER=stepper_z
  SAVE_CONFIG

[gcode_macro Z_CAL]
gcode:
    G28
    G1 X95 Y100
    G90
    Z_ENDSTOP_CALIBRATE
    TESTZ Z=-200

########################################
# PID Tuning Macros
########################################
       
[gcode_macro PID_Extruder_Fan_OFF_220]
gcode:  PID_Start
        PID_CALIBRATE HEATER=extruder TARGET=220  
        PID_End          
         
[gcode_macro PID_Extruder_Fan_OFF_260]
gcode:  PID_Start
        PID_CALIBRATE HEATER=extruder TARGET=260   
        PID_End              
                 
[gcode_macro PID_Extruder_Fan_ON_220]
gcode:  PID_Start
        PID_CALIBRATE HEATER=extruder TARGET=220     
        PID_End                
         
[gcode_macro PID_Extruder_Fan_ON_260]
gcode:  PID_Start                
        PID_CALIBRATE HEATER=extruder TARGET=260    
        PID_End

[gcode_macro PID_Bed_100]
gcode:  PID_Bed_Start                
        PID_CALIBRATE HEATER=heater_bed TARGET=100    
        PID_End 

[gcode_macro PID_Bed_60]
gcode:  PID_Bed_Start                
        PID_CALIBRATE HEATER=heater_bed TARGET=60   
        PID_End 

[gcode_macro PID_Start]
gcode:  G28
        G1 X100 Y100 Z2 F 2000
        M106

[gcode_macro PID_Bed_Start]
gcode:  G28
        M106

[gcode_macro PID_End]
gcode:  RESPOND PREFIX=tgnotify MSG="PID Tuning Complete"
        M107
        G28          
        M84     

# # # # # # # # # # # # # # # # # # #
# Tool change and selection
# # # # # # # # # # # # # # # # # # #

[gcode_macro CHANGE_FILAMENT]
gcode:
  G28
  M117 Heating extruder                    # Message on display
  M109 S220
  M83                                      # Relative moves for extruder
  G92 E0                                   # Set the current filament position to E=0
  M117 Unloading extruder                  # Message on display
  G1 F300 E-70                             # Quickly retract 50 mm to free the splitter
  G28                                      # Home to signal it is finished
  M84                                      # motor off to extract filament without opening latch
  M117 Ready for new filament              # Message on display
  RESPOND PREFIX=tgalarm MSG="Ready for filament"
  G4 P20000                                # Wait 20s to start loading filament
  _LOAD_FILAMENT
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

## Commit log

2020-10-13 BTT SKR1.4 holder for Ultimaker 2
    [um2_skr14_holder.stl]
2020-10-15 created folders like Voron structure
    [um2_skr14_holder.stl]
2020-10-16 Marlin 2.0 for UM2
    [Configuration.h, Configuration_adv.h]
2020-11-19 first klipper commit
    [machine.cfg, macros.cfg, printer.cfg]
2020-11-22 debuging
    Z height is ok
    [machine.cfg, macros.cfg, printer.cfg]
2020-11-24 added mesh
    [machine.cfg, printer.cfg]
2020-12-31 updated klipper files
    all klipper files on my Raspberry Pi as of today
    [bed.cfg, kiauh.cfg, machine.cfg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]
2021-02-10 Vibration Test
    Bed vibration test before the installation of the new optimized bed holder. The test was made with the Energetic magnetic steel sheet plate installed, which the added mass changed the resonance frequency and probably increased the vibrations. The new bed holder fixes this problem.
2022-08-27 updated klipper files
    [bed.cfg, kiauh.cfg, machine.cfg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]
2022-08-27 added data from FEA simulations for Z stage bed base plate
    [fusion360_sim_results.xlsx, z-stage_assembly_2 v13.f3z]
2022-08-27 moved movies to Z stage folder
2023-04-08 backup 08.04.2023
    [bed.cfg, machine.cfg, macros.cfg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]
2023-07-20 added Hextrudort E3D V6 BOM
2023-07-24 backup 24.07.2023
    [machine.cfg, macros.cfg, printer-20221127_235012.cfg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]
2023-10-12 added diode information at the mesh probe

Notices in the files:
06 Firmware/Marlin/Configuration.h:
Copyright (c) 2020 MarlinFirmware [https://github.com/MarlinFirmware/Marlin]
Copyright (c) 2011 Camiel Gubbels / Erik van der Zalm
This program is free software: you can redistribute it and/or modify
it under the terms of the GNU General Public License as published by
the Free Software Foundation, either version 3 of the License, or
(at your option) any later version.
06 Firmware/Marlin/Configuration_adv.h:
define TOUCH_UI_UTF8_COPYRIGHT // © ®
